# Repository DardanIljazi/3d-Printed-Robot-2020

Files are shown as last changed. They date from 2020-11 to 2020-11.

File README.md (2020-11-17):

# 3D Printed Robot

The goal is to make a little bluetooth robot commanded with a mobile application.

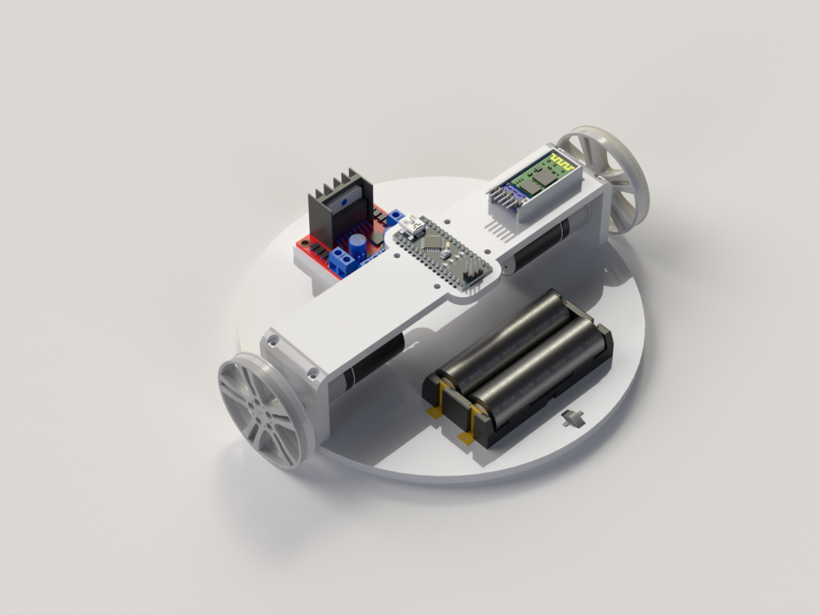
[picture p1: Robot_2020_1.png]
3D printed robot, 3d rendering


## Result

### Robot

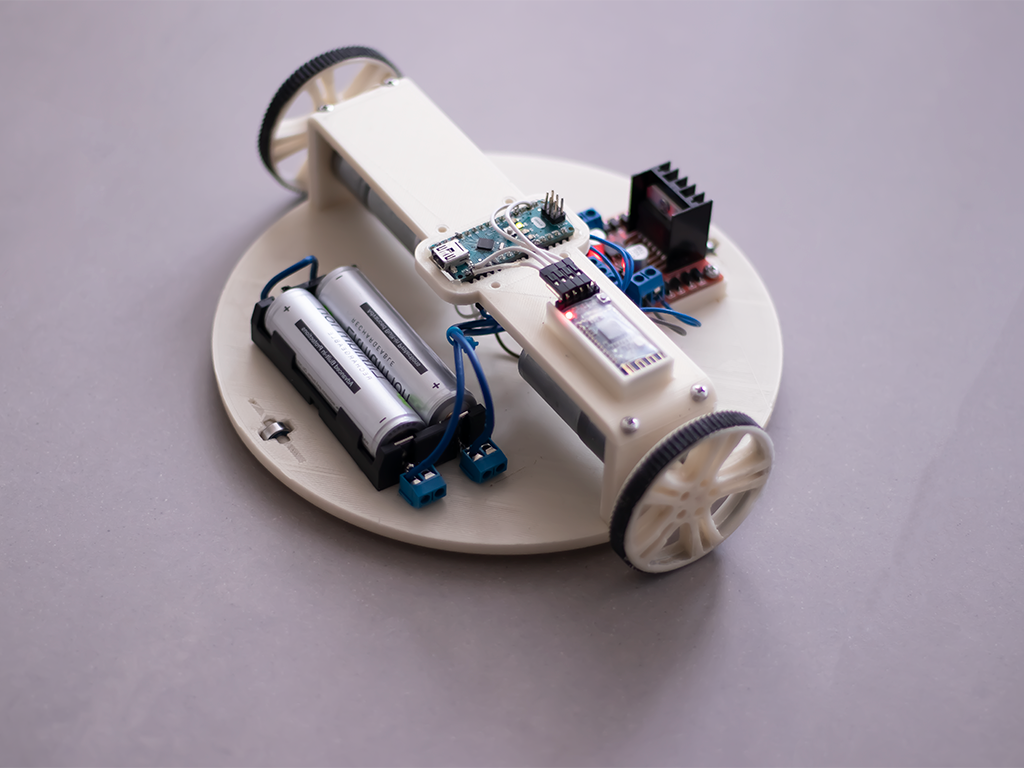
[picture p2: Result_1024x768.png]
3D printed Robot result


### Mobile application

*WIP: The app should and will be modified or changed by any other app already in Play/App store, the code has to be changed accordingly in Arduino nano*

## Parts and prices

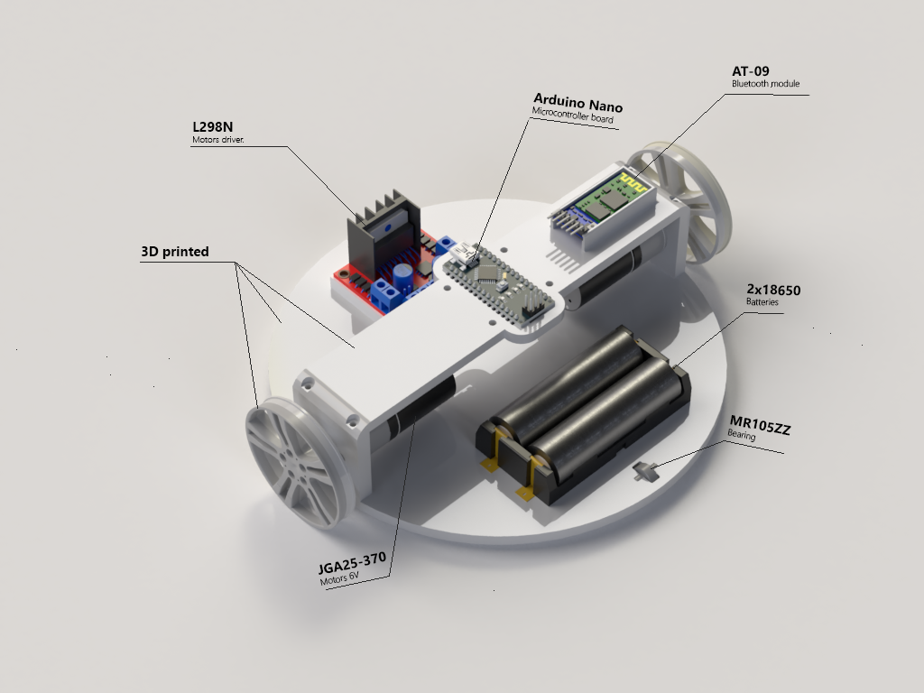
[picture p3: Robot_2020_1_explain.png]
3D printed robot, 3d rendering with titles for some parts


## Price: less than 35$ (shipping costs included)

Components have been chosen with 2 main parameters:

- **Best vendor** rating (only vendors equal or above 98% of positive feedback have been chosen)
- **Lowest price** found, including shipping cost

| Product | Name | Quantity | Price in $ | Get Product | Comment |
| :---: | --- | :---: | :---: | ---: | --- |
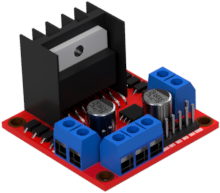
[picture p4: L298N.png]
L298n (https://s.click.aliexpress.com/e/_AUgiWD)
|  | L298N <br />Motors driver | 1 | 1.55 | [**Get**](https://s.click.aliexpress.com/e/_AUgiWD) | |
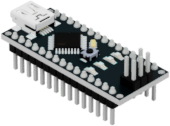
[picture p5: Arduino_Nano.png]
Arduino Nano (https://s.click.aliexpress.com/e/_An73jR)
|  | Arduino Nano<br />Microcontroller | 1 | 2.47 | [**Get**](https://s.click.aliexpress.com/e/_An73jR) | |
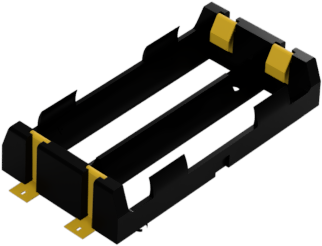
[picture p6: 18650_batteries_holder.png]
18650 batteries holder (https://s.click.aliexpress.com/e/_9RttAp)
|  | 18650 battery holder | 1 | 2 | [**Get**](https://s.click.aliexpress.com/e/_9RttAp) | |
| AT-09 (https://s.click.aliexpress.com/e/_A9LxwV) | AT-09<br />Bluetooth module | 1 | 1.63 | [**Get**](https://s.click.aliexpress.com/e/_A9LxwV) | |
| | Dupont wire <br />(*Female VS Female*, *10cm*, *10 pin*) | 1 | 0.54 | [**Get**](https://s.click.aliexpress.com/e/_98ks45) | Used to connect <br />AT-09 and L298N <br />with Arduino Nano pins |
| | Dupont wire <br />(*Male VS Male*, *10cm*, *10 pin*) | 1 | 0.74 | [**Get**](https://s.click.aliexpress.com/e/_98ks45) | Used to connect motors<br />and battery pins with L298N |
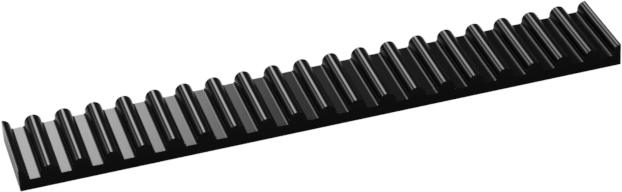
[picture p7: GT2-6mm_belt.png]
GT2-6mm belt (https://s.click.aliexpress.com/e/_Acf6TL)
|  | GT2-6mm belt | 1 | 0.69 | [**Get**](https://s.click.aliexpress.com/e/_Acf6TL) | |
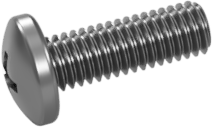
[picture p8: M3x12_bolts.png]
M3 bolts (https://s.click.aliexpress.com/e/_9yCjq9)
|  | M3x12 Bolts | 1 | 2.08 | [**Get**](https://s.click.aliexpress.com/e/_9yCjq9) | |
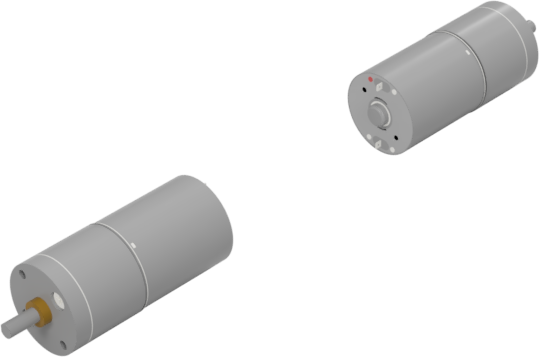
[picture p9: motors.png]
JGA25-370 motors (https://s.click.aliexpress.com/e/_AeoSBF)
|  | JGA25-370 motors | 2 | 7 | [**Get**](https://s.click.aliexpress.com/e/_AeoSBF) | |
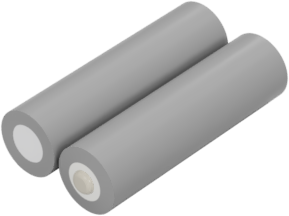
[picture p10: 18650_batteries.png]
18650 Batteries (https://s.click.aliexpress.com/e/_9xaDaV)
|  | 18650 LiitoKala 3500 mAh 3.7v<br />(*2pcs*) | 2 | 5.97 | [**Get**](https://s.click.aliexpress.com/e/_9xaDaV) | |
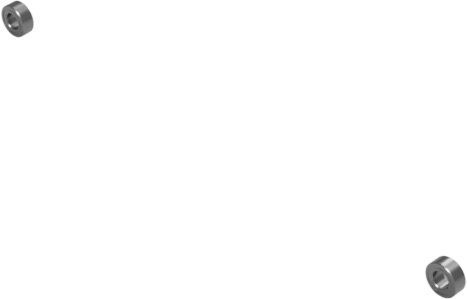
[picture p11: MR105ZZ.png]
MR105ZZ bearing (https://s.click.aliexpress.com/e/_AVCCDX)
|  | MR105ZZ Bearings | 1 | 3.10 | [**Get**](https://s.click.aliexpress.com/e/_AVCCDX) | Bearing to make the robot be flat on the floor, <br />this is **optional** <br />but is recommended so <br />robot doesn't lean on front or back |
| | **Total** |  **13**  | **27.77** | | Equals to ~:<br />- 25.40 CHF<br />- 23.50 € |
| | Shipping cost | | 7 | | Shipping cost is **approximatively ~$7** <br />(to Switzerland), <br />since this depends in which country you are, it could differ. |
| | **<u>Total with shipping</u>** | | **<u>34.77</u>** | | Equals to ~:<br />- 31.40 CHF<br />- 29.44 € |

# Documentation

## Printing 3D parts

Find parts to print in [Parts folder](Parts), they are already classified, print them with recommended printing settings below.

Default recommended printing settings are these:

- `Layer height`: `0.2 mm` 

- `Infill`: `50%`

- `Support`: `No`

- `Build plate adhesion`: `Brim`

- `Nozzle`: `0.4 mm`

| Picture of STL file | Name | Other printing settings | Number of prints |
| --- | :--- | :---: | :---: |
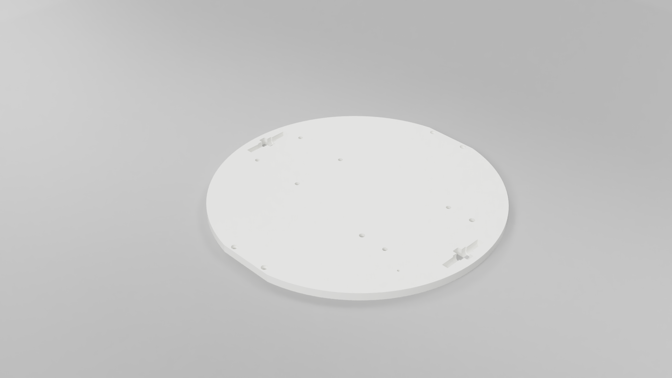
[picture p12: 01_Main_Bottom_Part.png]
01_Main_Bottom_Part
| <br /> | <br />[**01_Main_Bottom_Part.stl**](Parts/01_Main_Bottom_Part.stl) | <br />- | <br />1 |
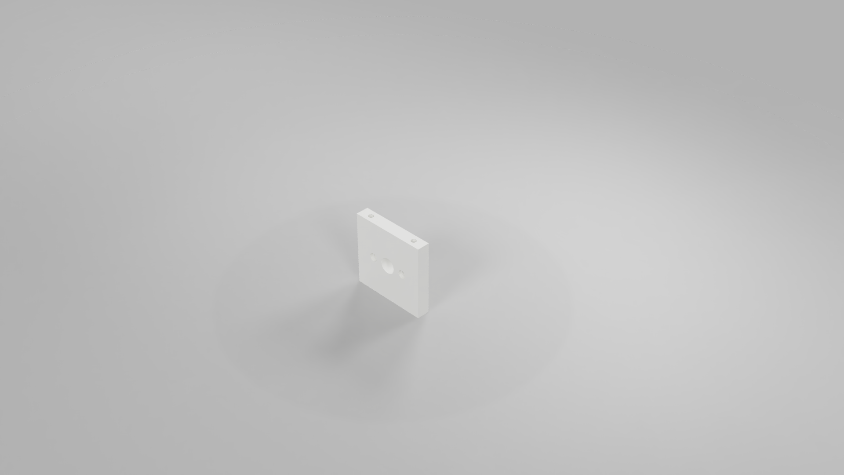
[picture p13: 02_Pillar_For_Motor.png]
02_Pillar_For_Motor
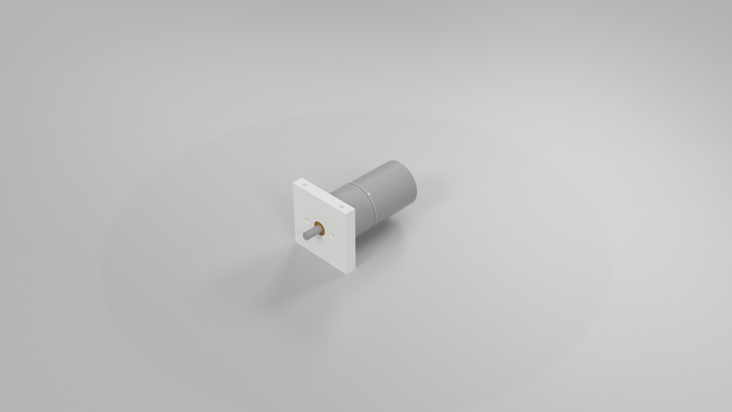
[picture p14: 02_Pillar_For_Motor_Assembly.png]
02_Pillar_For_Motor_Assembly
| <br /><br /> | <br />[**02_Pillar_For_Motor.stl**](Parts/02_Pillar_For_Motor.stl) | <br />- | <br />2 |
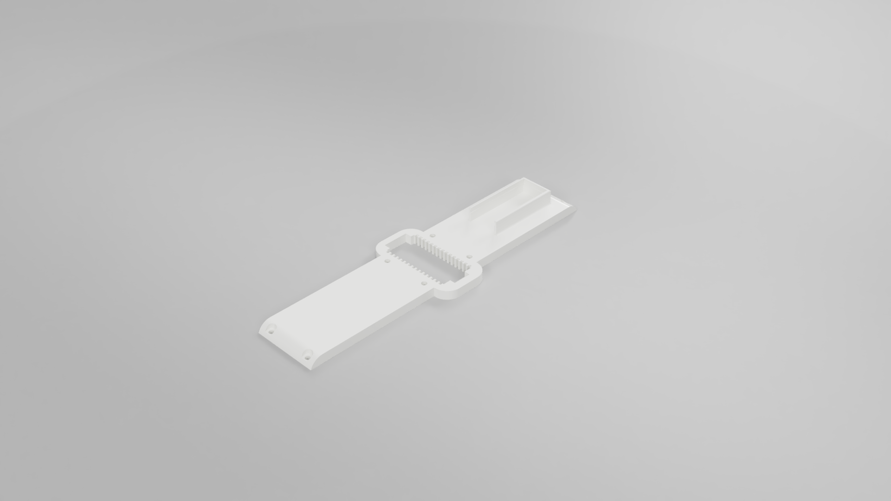
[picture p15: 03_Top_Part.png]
03_Top_Part
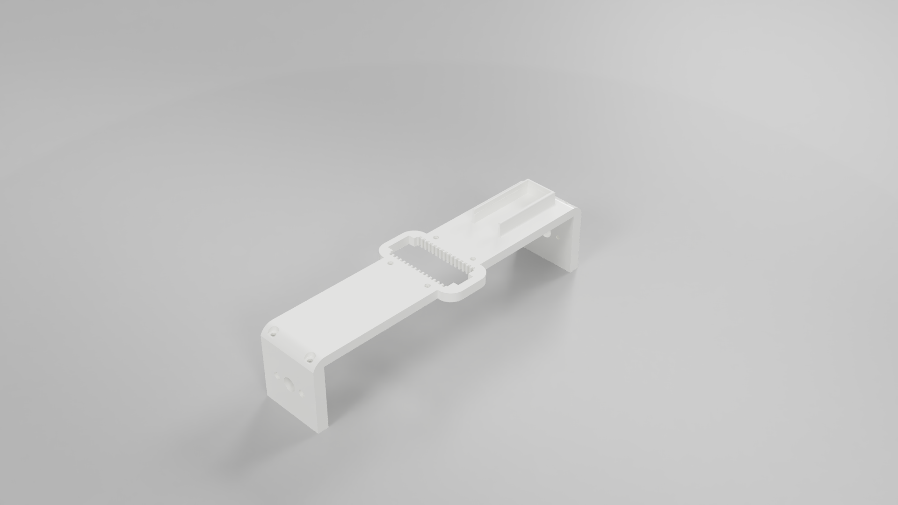
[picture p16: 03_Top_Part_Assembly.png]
03_Top_Part_Assembly
| <br /><br /> | <br />[**03_Top_Part.stl**](Parts/03_Top_Part.stl) | <br />- | <br />1 |
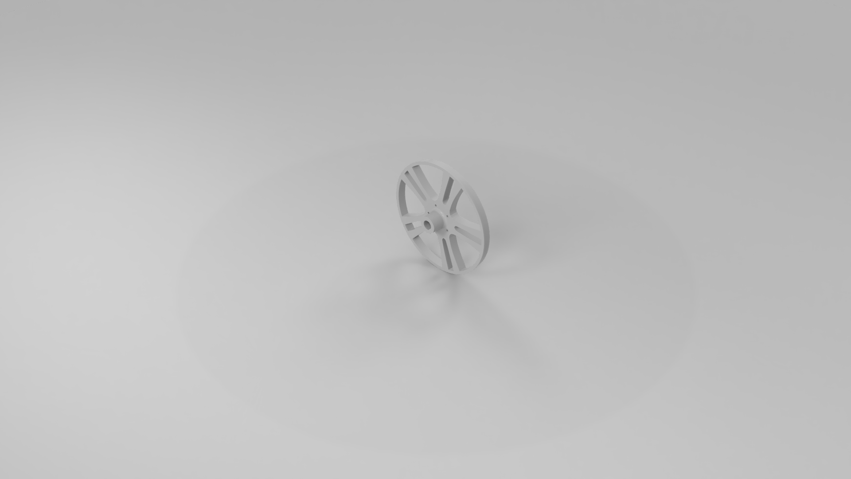
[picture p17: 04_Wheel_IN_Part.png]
04_Wheel_IN_Part
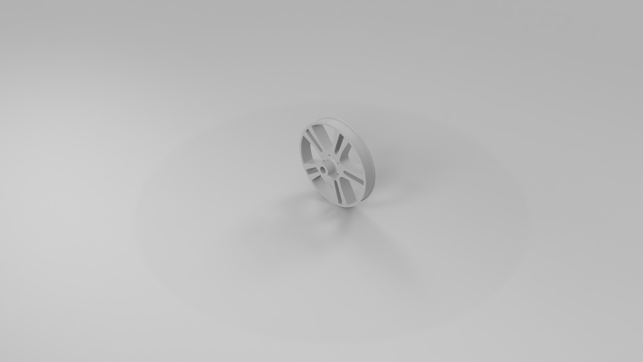
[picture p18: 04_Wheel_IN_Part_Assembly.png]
04_Wheel_IN_Part_Assembly
| <br /><br /> | <br />[**04_Wheel_IN_Part.stl**](Parts/04_Wheel_IN_Part.stl) | <br />- | <br />2 |
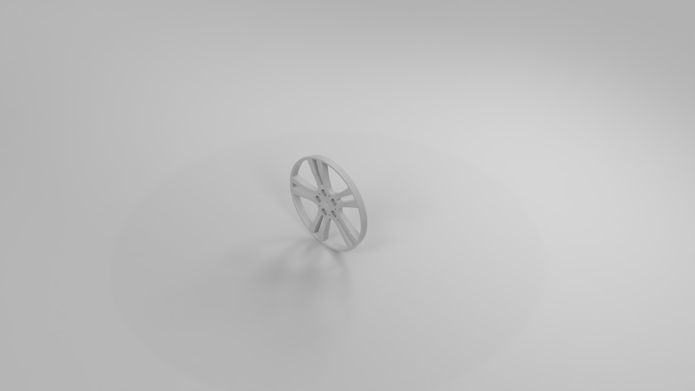
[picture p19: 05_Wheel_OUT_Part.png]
05_Wheel_OUT_Part
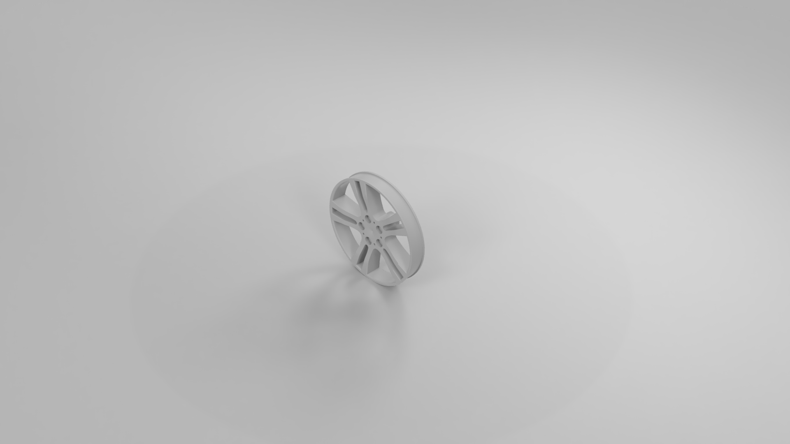
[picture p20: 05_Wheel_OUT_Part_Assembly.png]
05_Wheel_OUT_Part_Assembly
| <br /><br /> | <br />[**05_Wheel_OUT_Part.stl**](Parts/05_Wheel_OUT_Part.stl) | <br />`Layer height`: `0.05 mm` or if not possible: `0.1 mm` | <br />2 |
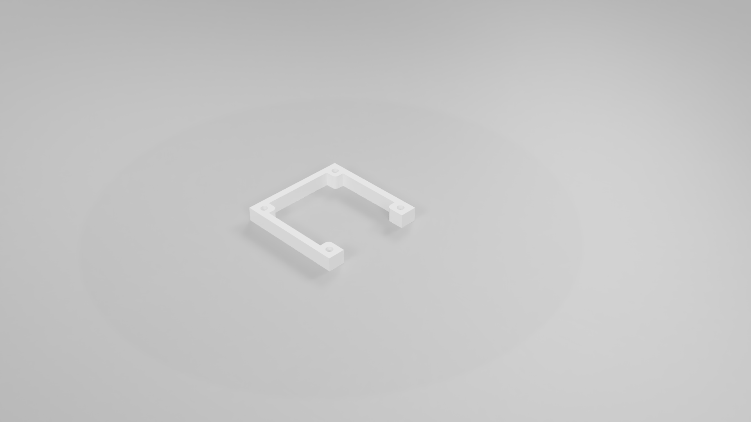
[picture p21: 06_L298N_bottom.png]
06_L298N_bottom
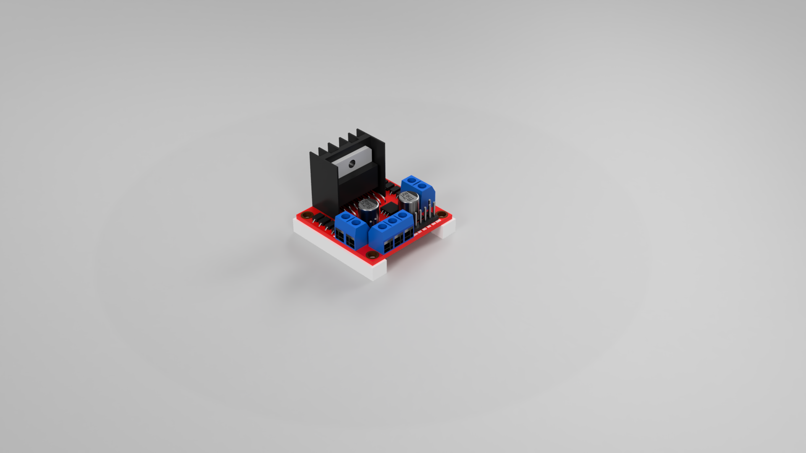
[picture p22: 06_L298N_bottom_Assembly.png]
06_L298N_bottom_Assembly
| <br /><br /> | <br />[**06_L298N_bottom.stl**](Parts/06_L298N_bottom.stl) | <br />- | <br />1 |
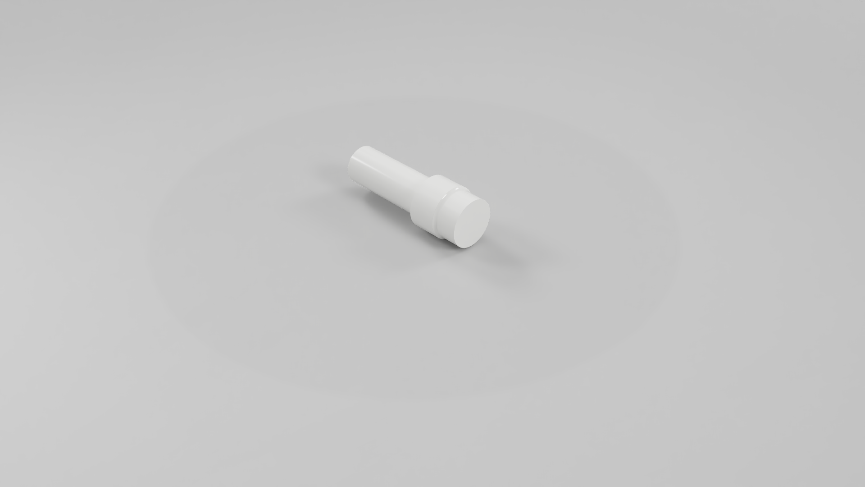
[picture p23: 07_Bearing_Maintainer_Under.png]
07_Bearing_Maintainer_Under
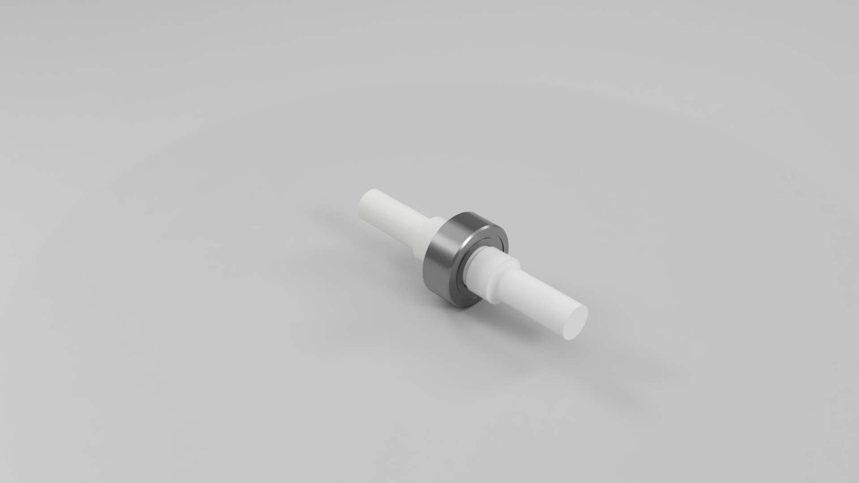
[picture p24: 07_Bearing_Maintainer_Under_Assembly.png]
07_Bearing_Maintainer_Under_Assembly
| <br /><br /> | <br />[**07_Bearing_Maintainer_Under.stl**](Parts/07_Bearing_Maintainer_Under.stl) | <br />`Layer height`: `0.05 mm` or if not possible: `0.1 mm` | <br />4 |

## After printing, before final assembly: Tapping

All holes for these pieces have to be tapped with M3 size. If you don't have a tapping tool, you can get one [here](https://s.click.aliexpress.com/e/_ANrDs1).

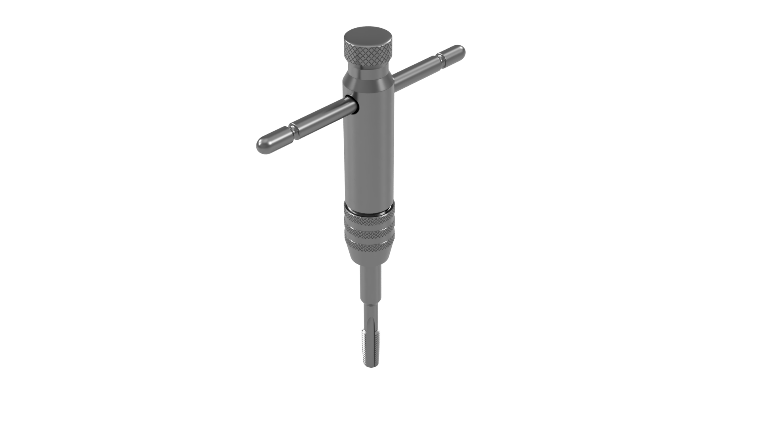
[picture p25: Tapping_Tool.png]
Tapping


| Illustration | Piece to tap |
| --- | --- |
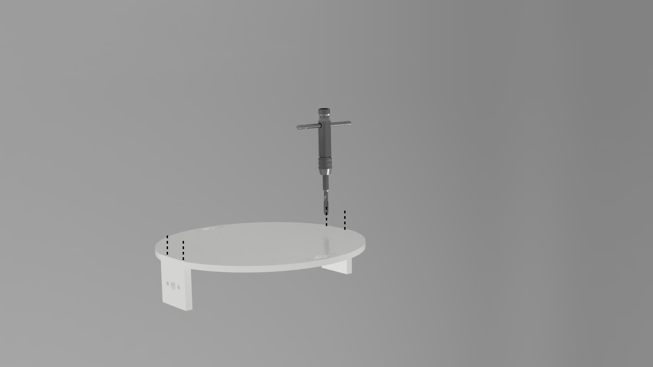
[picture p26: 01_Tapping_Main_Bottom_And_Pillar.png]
01_Tapping_Main_Bottom_And_Pillar
| <br /> | <br />Thread the two parts together, in order to have a screw that does not jam.<br />[**01_Main_Bottom_Part.stl**](Parts/01_Main_Bottom_Part.stl) <br />with<br />[**02_Pillar_For_Motor.stl**](Parts/02_Pillar_For_Motor.stl) |
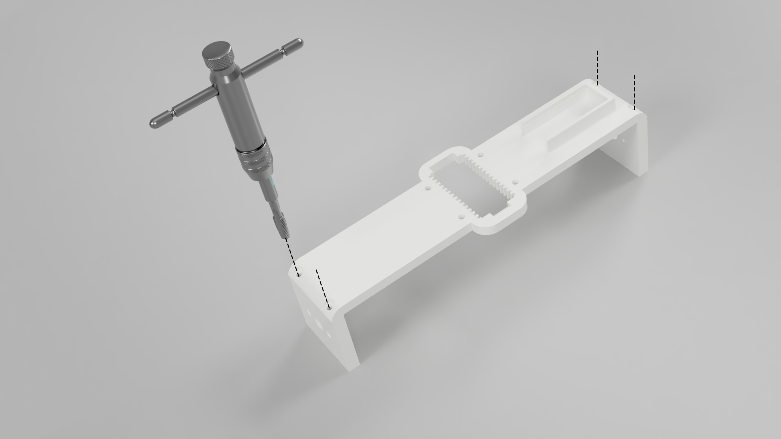
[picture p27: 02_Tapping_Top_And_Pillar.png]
02_Tapping_Top_And_Pillar
| <br /> | <br />Thread the two parts together, in order to have a screw that does not jam.<br />[**03_Top_Part.stl**](Parts/03_Top_Part.stl) <br />with<br />[**02_Pillar_For_Motor.stl**](Parts/02_Pillar_For_Motor.stl) |
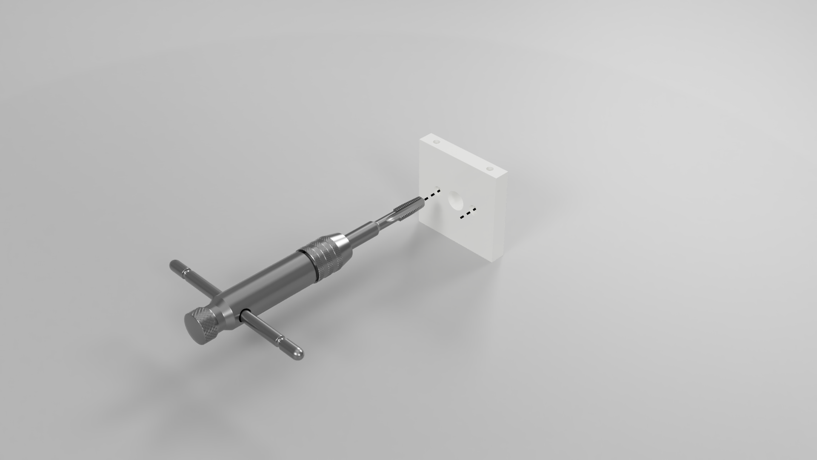
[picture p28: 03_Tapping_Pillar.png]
03_Tapping_Pillar
| <br /> | <br />[**02_Pillar_For_Motor.stl**](Parts/02_Pillar_For_Motor.stl) |
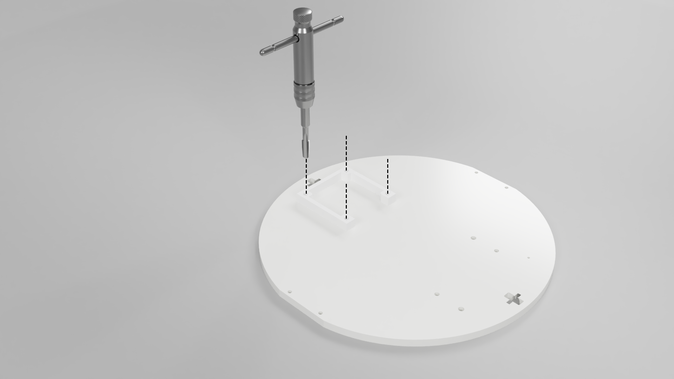
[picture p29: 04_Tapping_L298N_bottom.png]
04_Tapping_L298N_Bottom
| <br /> | <br />[**06_L298N_bottom.stl**](Parts/06_L298N_bottom.stl) |

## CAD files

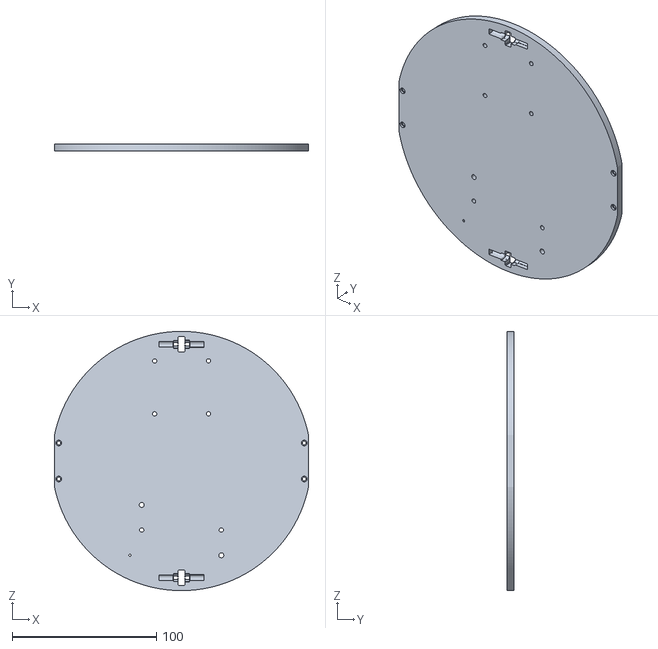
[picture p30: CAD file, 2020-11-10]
Parts/01_Main_Bottom_Part.stl
176.4 x 5.00 x 180.0

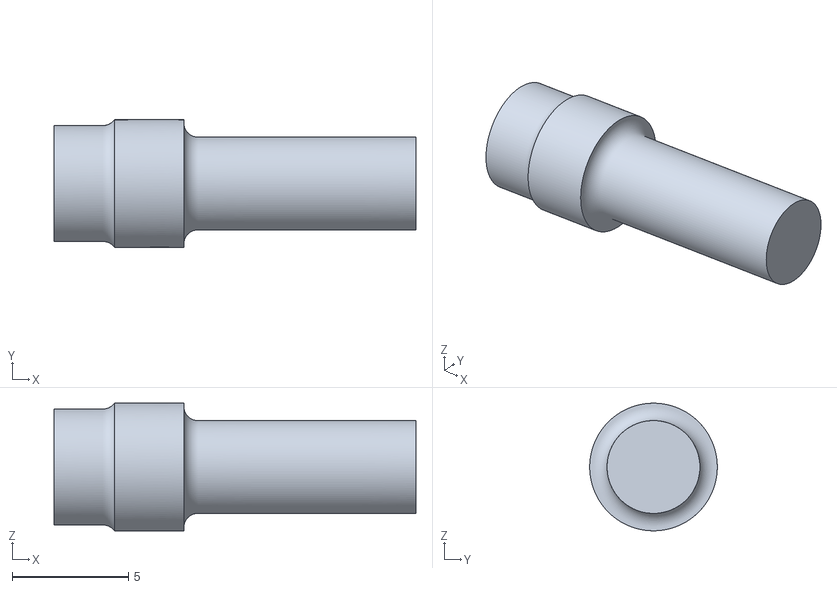
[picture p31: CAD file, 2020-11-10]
Parts/07_Bearing_Maintainer_Under.stl
15.6 x 5.50 x 5.50

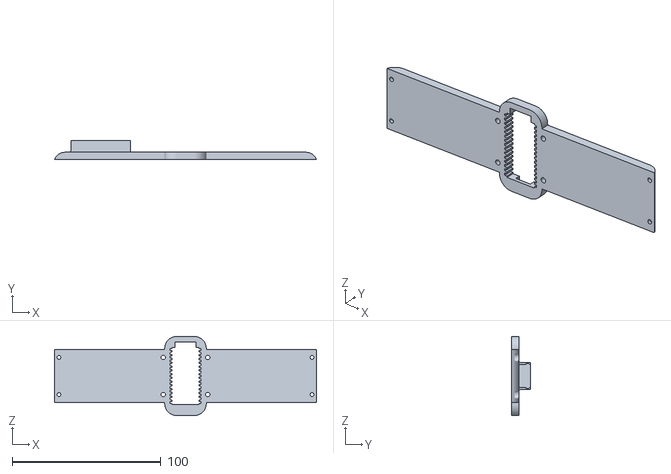
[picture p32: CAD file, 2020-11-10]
Parts/03_Top_Part.stl
176.4 x 13.0 x 53.2

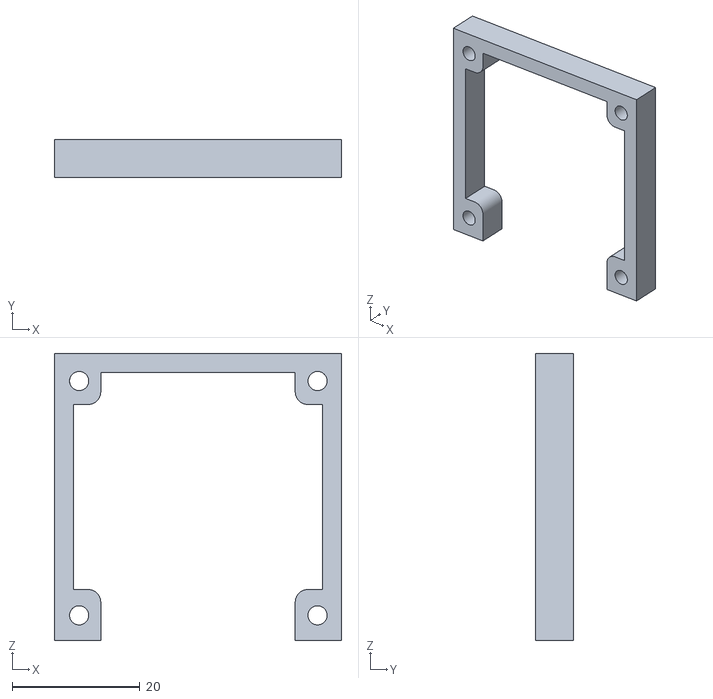
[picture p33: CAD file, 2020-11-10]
Parts/06_L298N_bottom.stl
45.0 x 6.00 x 45.0

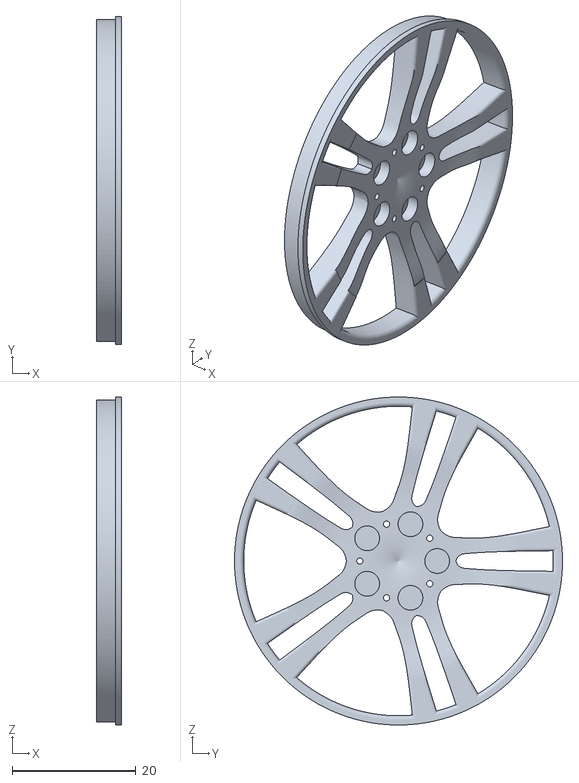
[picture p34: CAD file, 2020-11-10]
Parts/05_Wheel_OUT_Part.stl
4.00 x 53.0 x 53.0

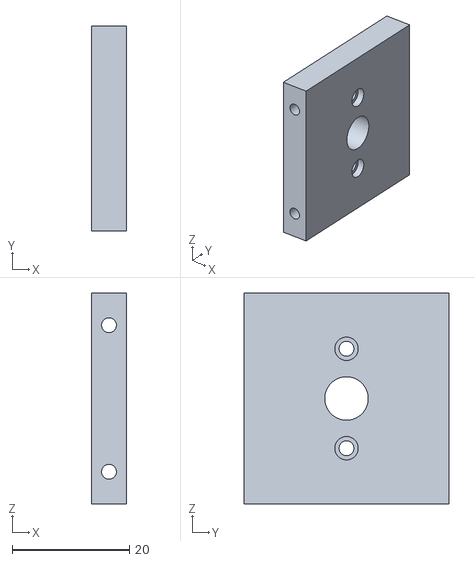
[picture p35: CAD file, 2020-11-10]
Parts/02_Pillar_For_Motor.stl
6.00 x 35.0 x 36.0

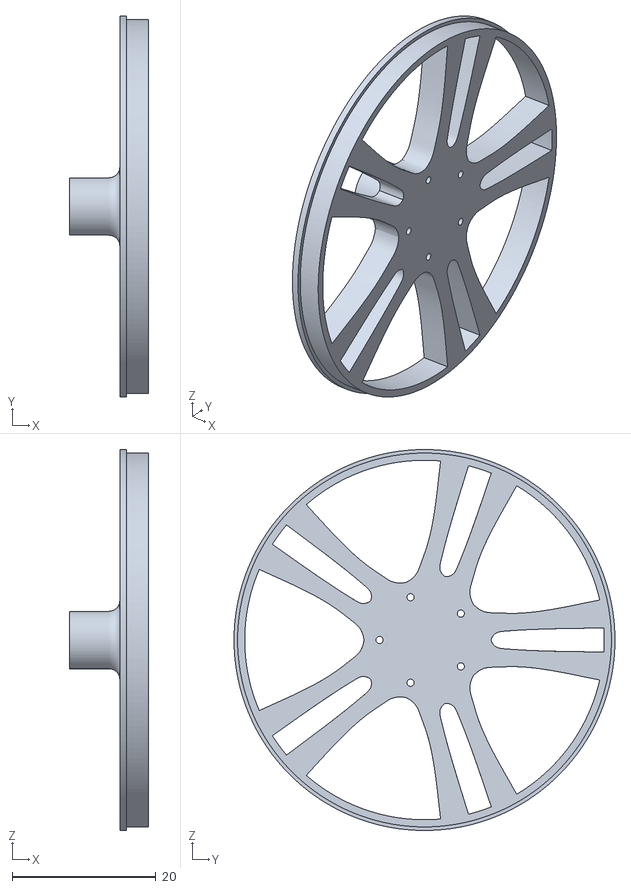
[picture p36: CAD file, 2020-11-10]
Parts/04_Wheel_IN_Part.stl
11.0 x 53.0 x 53.0

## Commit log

2020-11-10 Add parts to print in stl format
    [01_Main_Bottom_Part.stl, 02_Pillar_For_Motor.stl, 03_Top_Part.stl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]
2020-11-12 Typo and begin after printing part
